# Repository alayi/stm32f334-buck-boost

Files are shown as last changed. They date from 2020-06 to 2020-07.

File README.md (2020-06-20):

## Buck-boost преобразователь с цифровым управлением

Преобразователь построен на базе микроконтроллера STM32F334C4 с аппаратным модулем HRPWM с возможностью работы на частотах от 100 до 2000 кГц, в зависимости от примененных драйверов и транзисторов. В источнике питания реализованы аппаратные защиты по току и другие, что позволяет значительно повысить надежность работы. Для отладки выведены на разъем интерфейсы SWD и UART-TX, что позволяет производить real-time отладку через средства freeMaster и стандартный printf.

Вид платы (https://habrastorage.org/webt/9y/gj/tb/9ygjtbmnwvxfb2rbhex7k384b44.jpeg)

## Технические характеристики

* Топология: *buck-boost*
* Входное напряжение: *3...15В*
* Выходное напряжение: *3...15В*
* Стабилизация напряжения: *±0,5%*
* Номинальный ток: *5А*
* Стабилизация тока: *±2%* 
* Частота коммутации: *200 кГц*
* Алгоритмы: *CC/CV*
* КПД: *не менее 92%*
* Защиты: *OCP, OVP, UVLO, перегрев*
* Диапазон температур: *-40...+85 <sup>о</sup>C*
* Габариты: *52х50х8 мм*

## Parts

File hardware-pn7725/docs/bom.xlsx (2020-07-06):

Designator | Value | PartNumber | Manufacturer | Quantity | Comment | HelpURL
C1, C2 | 0.47μF | CL21B474KAFNNNG | Samsung | 2 | Ceramic capacitor, 0.47μF, X7R, ±10%, 25V, 805, -55...+125°C | https://www.digikey.com/product-detail/en/samsung-electro-mechanics/CL21B474KAFNNNG/1276-6480-1-ND/5958108
C3, C4, C7, C8 | 10μF | CL32B106KAJNNNE | Samsung | 4 | Ceramic capacitor, 10μF, X7R, ±10%, 25V, 1210, -55...+125°C | https://www.digikey.com/product-detail/en/samsung-electro-mechanics/CL32B106KAJNNNE/1276-1807-1-ND/3889893
C5, C6, C13, C14, C15, C16, C24, C25 | 1μF | CL10B105KA8NNNC | Samsung | 8 | Ceramic capacitor, 1μF, X7R, ±10%, 25V, 603, -55...+125°C | https://www.digikey.com/product-detail/en/samsung-electro-mechanics/CL10B105KA8NNNC/1276-1184-1-ND/3889270
C9, C10, C11, C12, C23 | 0.01μF | CL10B103KB8NNNC | Yageo | 5 | Ceramic capacitor, 0.01μF, X7R, ±10%, 50V, 603, -55...+125°C | https://www.digikey.com/product-detail/en/samsung-electro-mechanics/CL10B103KB8NNNC/1276-1009-1-ND/3889095
C17, C18, C19, C20, C21, C22, C26, C29, C30 | 0.1μF | CL10B104KB8WPND | Yageo | 9 | Ceramic capacitor, 0.1μF, X7R, ±10%, 50V, 603, -55...+125°C | https://www.digikey.com/product-detail/en/samsung-electro-mechanics/CL10B104KB8WPND/1276-CL10B104KB8WPNDCT-ND/11488014
C27, C28 | 12pF | CL10C120JB8NNNC | Samsung | 2 | Ceramic capacitor, 12pF, NPO, ±10%, 50V, 603, -55...+125°C | https://www.digikey.com/product-detail/en/samsung-electro-mechanics/CL10C120JB8NNNC/1276-1254-1-ND/3889340
D1, D2 |  | PN7725 | Chipown | 2 | Half-bridge module, 2N channel, 200kHz, 15W, supply 4...20V, -40...+125°C, 8-SOIC-PAD | http://chipown.com/product.asp?id=416
D3, D4 |  | INA199A1DCKR | Texas Instruments | 2 | IC current monitor, ±1.5%, 50V/V, -0.3...+26V, -40...+125°C, SOT23-5 | https://www.digikey.com/product-detail/en/texas-instruments/INA199A1DCKR/296-27329-1-ND/2279290
D5 |  | AP3012KTR-G1 | Diodes Incorporated | 1 | DC/DC boost converter, input 2.6...16V, 1.5MHz, output 3...29V, 0.5A, -40...+85°C, SOT23-5 | https://www.digikey.com/product-detail/en/diodes-incorporated/AP3012KTR-G1/AP3012KTR-G1DICT-ND/4505297
D6 |  | AP2204K-3.3TRG1 | Diodes Incorporated | 1 | Linear voltage regulator, input 4...24V, 0.5V, output 3.3V, 0.15A, -40...+85°C, SOT23-6 | https://www.digikey.com/product-detail/en/diodes-incorporated/AP2204K-3.3TRG1/AP2204K-3.3TRG1DICT-ND/4505288
D7 |  | STM32F334C4T6 | STMicroelectronics | 1 | IC microcontroller, 32-Bit, Cortex-M4, 72MHz, 16KB, 12KB, 2...3.6V, -40...+85°C, 48-LQFP | https://www.digikey.com/products/en?keywords=STM32F334C4T6
D8 |  | AP2204K-5.0TRG1 | Diodes Incorporated | 1 | Linear voltage regulator, input 4...24V, 0.5V, output 5V, 0.15A, -40...+85°C, SOT23-6 | https://www.digikey.com/product-detail/en/diodes-incorporated/AP2204K-5-0TRG1/AP2204K-5-0TRG1DICT-ND/4505289
L1 | 10μH | SDR1006-100ML | Bourns | 1 | Fixed inductor, 10μH, ±20%, SDR0805, 2.6A, -40...+125°C | https://www.digikey.com/product-detail/en/bourns-inc/SDR1006-100ML/SDR1006-100MLCT-ND/2127202
L2 | 10μH | SDR0403-100ML | Bourns | 1 | Fixed inductor, 10μH, ±20%, SDR0403, 1.15A, -40...+125°C | https://www.digikey.com/product-detail/en/bourns-inc/SDR0403-100ML/SDR0403-100MLCT-ND/2127080
L3 | 10μH | LQM18FN100M00D | Murata Electronics | 1 | Fixed inductor, 10μH, ±20%, 603, 50mA, -55...+125°C | https://www.digikey.com/product-detail/en/murata-electronics-north-america/LQM18FN100M00D/490-4025-1-ND/1016285
R5, R9 | 0R015 | PE2512FKE7W0R015L | Yageo | 2 | Resistor film, 0R015, ±1%, 2512, 2W, -55...+170°C | https://www.digikey.com/product-detail/en/yageo/PE2512FKE7W0R015L/YAG2165CT-ND/5139613
R6, R7 | 39k | RC0603FR-0739KL | Yageo | 2 | Resistor film, 39k, ±1%, 603, 0.1W, -55...+125°C | https://www.digikey.com/product-detail/en/yageo/RC0603FR-0739KL/311-39-0KHRCT-ND/730142
R8, R10 | 120R | RC0603JR-07120RL | Yageo | 2 | Resistor film, 120R, ±5%, 603, 0.1W, -55...+125°C | https://www.digikey.com/product-detail/en/yageo/RC0603JR-07120RL/311-120GRCT-ND/729653
R11, R12, R16 | 10k | RC0603FR-0710KL | Yageo | 3 | Resistor film, 10k, ±1%, 603, 0.1W, -55...+125°C | https://www.digikey.com/product-detail/en/yageo/RC0603FR-0710KL/311-10-0KHRCT-ND/729827
R13, R15, R19, R20, R21 | 10k | RC0603JR-0710KL | Yageo | 5 | Resistor film, 10k, ±5%, 603, 0.1W, -55...+125°C | https://www.digikey.com/product-detail/en/yageo/RC0603JR-0710KL/311-10KGRCT-ND/729647
R14 | 110k | RC0603FR-07110KL | Yageo | 1 | Resistor film, 110k, ±1%, 603, 0.1W, -55...+125°C | https://www.digikey.com/product-detail/en/yageo/RC0603FR-07110KL/311-110KHRCT-ND/729852
R17, R18 | 1k | RC0603FR-071KL | Yageo | 2 | Resistor film, 1k, ±1%, 603, 0.1W, -55...+125°C | https://www.digikey.com/product-detail/en/yageo/RC0603FR-071KL/311-1-00KHRCT-ND/729790
VD1 |  | B160S1F-7 | Diodes Incorporated | 1 | Schottky diode, 60B160S1F-7, 1A, 650mV, 45pF, SOD-123F, -55...+150°C | https://www.digikey.com/product-detail/en/diodes-incorporated/B160S1F-7/B160S1F-7DICT-ND/7784161
VD2 |  | 150060BS75000 | Wurth | 1 | LED, 20mA, 3.2V, 603, -55...+150°C | https://www.digikey.com/product-detail/en/w-rth-elektronik/150060BS75000/732-4966-1-ND/4489893
VD3 |  | 150060RS75000 | Wurth | 1 | LED, 20 mA, 2V, 603, -55...+150°C | https://www.digikey.com/product-detail/en/w-rth-elektronik/150060RS75000/732-4978-1-ND/4489899
X1, X2, X3, X4 |  | 8191 | Keystone | 4 | Power connector, 500V, 15A | https://ru.mouser.com/ProductDetail/Keystone-Electronics/8191?qs=lQmX4aIt5iAMQ8PQTpZ%2Fwg%3D%3D
X5 |  | SM05B-GHS | JST | 1 | Connector, 5pin, 1.25mm, 50VDC, 1A | https://www.digikey.com/product-detail/en/jst-sales-america-inc/SM05B-GHS-TB-LF-SN/455-1567-1-ND/807835
Z1 |  | ECS-80-12-33-JGN-TR | ECS | 1 | Crystal, 8MHz, 12pF, ±30ppm, case 3225, -40...+85°C | https://www.digikey.com/product-detail/en/ecs-inc/ECS-80-12-33-JGN-TR/50-ECS-80-12-33-JGN-CT-ND/10478769

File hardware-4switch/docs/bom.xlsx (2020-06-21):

Designator | Value | PartNumber | Manufacturer | Quantity | Comment | HelpURL
C1, C2 | 0.47μF | CL21B474KAFNNNG | Samsung | 2 | Ceramic capacitor, 0.47μF, X7R, ±10%, 25V, 0805, -55...+125°C | https://www.digikey.com/product-detail/en/samsung-electro-mechanics/CL21B474KAFNNNG/1276-6480-1-ND/5958108
C3, C4, C17, C18, C19, C20, C26, C27 | 1μF | CL10B105KA8NNNC | Samsung | 8 | Ceramic capacitor, 1μF, X7R, ±10%, 25V, 0603, -55...+125°C | https://www.digikey.com/product-detail/en/samsung-electro-mechanics/CL10B105KA8NNNC/1276-1184-1-ND/3889270
C5, C6, C7, C8, C9, C10 | 10μF | CL32B106KAJNNNE | Samsung | 6 | Ceramic capacitor, 10μF, X7R, ±10%, 25V, 1210, -55...+125°C | https://www.digikey.com/product-detail/en/samsung-electro-mechanics/CL32B106KAJNNNE/1276-1807-1-ND/3889893
C11, C12, C15, C16, C25 | 0.01μF | CL10B103KB8NNNC | Yageo | 5 | Ceramic capacitor, 0.01μF, X7R, ±10%, 50V, 0603, -55...+125°C | https://www.digikey.com/product-detail/en/samsung-electro-mechanics/CL10B103KB8NNNC/1276-1009-1-ND/3889095
C13, C14 | 470pF | CL10C471JB8NNNC | Yageo | 2 | Ceramic capacitor, 470pF, NPO, ±5%, 50V, 0603, -55...+125°C | https://www.digikey.com/product-detail/en/samsung-electro-mechanics/CL10C471JB8NNNC/1276-1168-1-ND/3889254
C21, C22, C23, C24, C28, C31, C32 | 0.1μF | CL10B104KB8WPND | Yageo | 7 | Ceramic capacitor, 0.1μF, X7R, ±10%, 50V, 0603, -55...+125°C | https://www.digikey.com/product-detail/en/samsung-electro-mechanics/CL10B104KB8WPND/1276-CL10B104KB8WPNDCT-ND/11488014
C29, C30 | 12pF | CL10C120JB8NNNC | Samsung | 2 | Ceramic capacitor, 12pF, NPO, ±10%, 50V, 0603, -55...+125°C | https://www.digikey.com/product-detail/en/samsung-electro-mechanics/CL10C120JB8NNNC/1276-1254-1-ND/3889340
D1, D2 |  | FD2105M | Fortior Tech | 2 | Half-bridge gate driver, 40V, +1.2A/-1.8A, Complementary, supply 3...21V, -40...+125°C, 10-MSOP | https://lcsc.com/product-detail/Others_Fortior-Tech-FD2105M_C328452.html
D3, D4 |  | TSV991ILT | STMicroelectronics | 2 | IC op amplifier, Rail-to-Rail, 20 MHz, 2.7...5.5V, -40...+125°C, SOT23-5 | https://www.digikey.com/product-detail/en/stmicroelectronics/TSV991ILT/497-6001-1-ND/1578484
D5 |  | AP3012KTR-G1 | Diodes Incorporated | 1 | DC/DC boost converter, input 2.6...16V, 1.5MHz, output 3...29V, 0.5A, -40...+85°C, SOT23-5 | https://www.digikey.com/product-detail/en/diodes-incorporated/AP3012KTR-G1/AP3012KTR-G1DICT-ND/4505297
D6 |  | STM32F334C4T6 | STMicroelectronics | 1 | IC microcontroller, 32-Bit, Cortex-M4, 72MHz, 16KB, 12KB, 2...3.6V, -40...+85°C, 48-LQFP | https://www.digikey.com/products/en?keywords=STM32F334C4T6
D7 |  | AP2204K-3.3TRG1 | Diodes Incorporated | 1 | Linear voltage regulator, input 4...24V, 0.5V, output 3.3V, 0.15A, -40...+85°C, SOT23-6 | https://www.digikey.com/product-detail/en/diodes-incorporated/AP2204K-3.3TRG1/AP2204K-3.3TRG1DICT-ND/4505288
L1 | 10μH | SRP1038C-100M | Bourns | 1 | Fixed inductor, 10μH, ±20%, SRP1038C, 8.5A, -40...+125°C | https://www.digikey.com/product-detail/en/bourns-inc/SRP1038C-100M/SRP1038C-100MCT-ND/10249149
L2 | 10μH | SDR0403-100ML | Bourns | 1 | Fixed inductor, 10μH, ±20%, SDR0403, 1.15A, -40...+125°C | https://www.digikey.com/product-detail/en/bourns-inc/SDR0403-100ML/SDR0403-100MLCT-ND/2127080
L3 | 10μH | LQM18FN100M00D | Murata Electronics | 1 | Fixed inductor, 10μH, ±20%, 0603, 50mA, -55...+125°C | https://www.digikey.com/product-detail/en/murata-electronics-north-america/LQM18FN100M00D/490-4025-1-ND/1016285
R1, R2, R5, R6 | 10R | RC0603JR-0710RL | Yageo | 4 | Resistor film, 10R, ±5%, 0603, 0.1W, -55...+125°C | https://www.digikey.com/product-detail/en/yageo/RC0603JR-0710RL/311-10GRCT-ND/729646
R3, R4, R7, R8, R11, R12, R13, R14, R35, R42, R43, R46 | 10k | RC0603JR-0710KL | Yageo | 12 | Resistor film, 10k, ±5%, 0603, 0.1W, -55...+125°C | https://www.digikey.com/product-detail/en/yageo/RC0603JR-0710KL/311-10KGRCT-ND/729647
R9, R10 | 120k | RC0603JR-07120KL | Yageo | 2 | Resistor film, 120k, ±5%, 0603, 0.1W, -55...+125°C | https://www.digikey.com/product-detail/en/yageo/RC0603JR-07120KL/311-120KGRCT-ND/729654
R15, R16 | 39k | RC0603FR-0739KL | Yageo | 2 | Resistor film, 39k, ±1%, 0603, 0.1W, -55...+125°C | https://www.digikey.com/product-detail/en/yageo/RC0603FR-0739KL/311-39-0KHRCT-ND/730142
R17, R18, R39 | 10k | RC0603FR-0710KL | Yageo | 3 | Resistor film, 10k, ±1%, 0603, 0.1W, -55...+125°C | https://www.digikey.com/product-detail/en/yageo/RC0603FR-0710KL/311-10-0KHRCT-ND/729827
R19, R20, R33, R34 | 20k | RC0603FR-0720KL | Yageo | 4 | Resistor film, 20k, ±1%, 0603, 0.1W, -55...+125°C | https://www.digikey.com/product-detail/en/yageo/RC0603FR-0720KL/311-20-0KHRCT-ND/729987
R21, R22, R23, R24, R29, R30, R31, R32, R36, R37, R40, R41, R44, R45 | 1k | RC0603FR-071KL | Yageo | 14 | Resistor film, 1k, ±1%, 0603, 0.1W, -55...+125°C | https://www.digikey.com/product-detail/en/yageo/RC0603FR-071KL/311-1-00KHRCT-ND/729790
R25, R26 | 120R | RC0603JR-07120RL | Yageo | 2 | Resistor film, 120R, ±5%, 0603, 0.1W, -55...+125°C | https://www.digikey.com/product-detail/en/yageo/RC0603JR-07120RL/311-120GRCT-ND/729653
R27, R28 | 0R05 | CRA2512-FZ-R050ELF | Bourns | 2 | Resistor film, 0R05, ±1%, 2512, 3W, -55...+170°C | https://www.digikey.com/product-detail/en/bourns-inc/CRA2512-FZ-R050ELF/CRA2512-FZ-R050ELFCT-ND/1775057
R38 | 110k | RC0603FR-07110KL | Yageo | 1 | Resistor film, 110k, ±1%, 0603, 0.1W, -55...+125°C | https://www.digikey.com/product-detail/en/yageo/RC0603FR-07110KL/311-110KHRCT-ND/729852
VD1, VD2, VD3 |  | B160S1F-7 | Diodes Incorporated | 3 | Schottky diode, 60B160S1F-7, 1A, 650mV, 45pF, SOD-123F, -55...+150°C | https://www.digikey.com/product-detail/en/diodes-incorporated/B160S1F-7/B160S1F-7DICT-ND/7784161
VD4, VD5 |  | 150060VS75000 | Wurth | 2 | LED, 20mA, 2V, 0603, -55...+150°C | https://www.digikey.com/product-detail/en/w-rth-elektronik/150060VS75000/732-4980-1-ND/4489904
VD6 |  | 150060BS75000 | Wurth | 1 | LED, 20mA, 3.2V, 0603, -55...+150°C | https://www.digikey.com/product-detail/en/w-rth-elektronik/150060BS75000/732-4966-1-ND/4489893
VD7, VD8, VD9 |  | 150060RS75000 | Wurth | 3 | LED, 20 mA, 2V, 0603, -55...+150°C | https://www.digikey.com/product-detail/en/w-rth-elektronik/150060RS75000/732-4978-1-ND/4489899
VT1, VT2, VT3, VT4 |  | BSC0904NSIATMA1 | Infineon Technologies | 4 | MOSFET N-channel transistor, 30V, 20A, 17nC, 2.5W, 3.7mOhm, 1100pF, 8-TDSON, -55...+150°C | https://www.digikey.com/product-detail/en/infineon-technologies/BSC0904NSIATMA1/BSC0904NSIATMA1CT-ND/3196475
X1, X2, X3, X4 |  | 8191 | Keystone | 4 | Power connector, 500V, 15A | https://ru.mouser.com/ProductDetail/Keystone-Electronics/8191?qs=lQmX4aIt5iAMQ8PQTpZ%2Fwg%3D%3D
X5 |  | SM05B-GHS | JST | 1 | Connector, 5pin, 1.25mm, 50VDC, 1A | https://www.digikey.com/product-detail/en/jst-sales-america-inc/SM05B-GHS-TB-LF-SN/455-1567-1-ND/807835
Z1 |  | ECS-80-12-33-JGN-TR | ECS | 1 | Crystal, 8MHz, 12pF, ±30ppm, case 3225, -40...+85°C | https://www.digikey.com/product-detail/en/ecs-inc/ECS-80-12-33-JGN-TR/50-ECS-80-12-33-JGN-CT-ND/10478769

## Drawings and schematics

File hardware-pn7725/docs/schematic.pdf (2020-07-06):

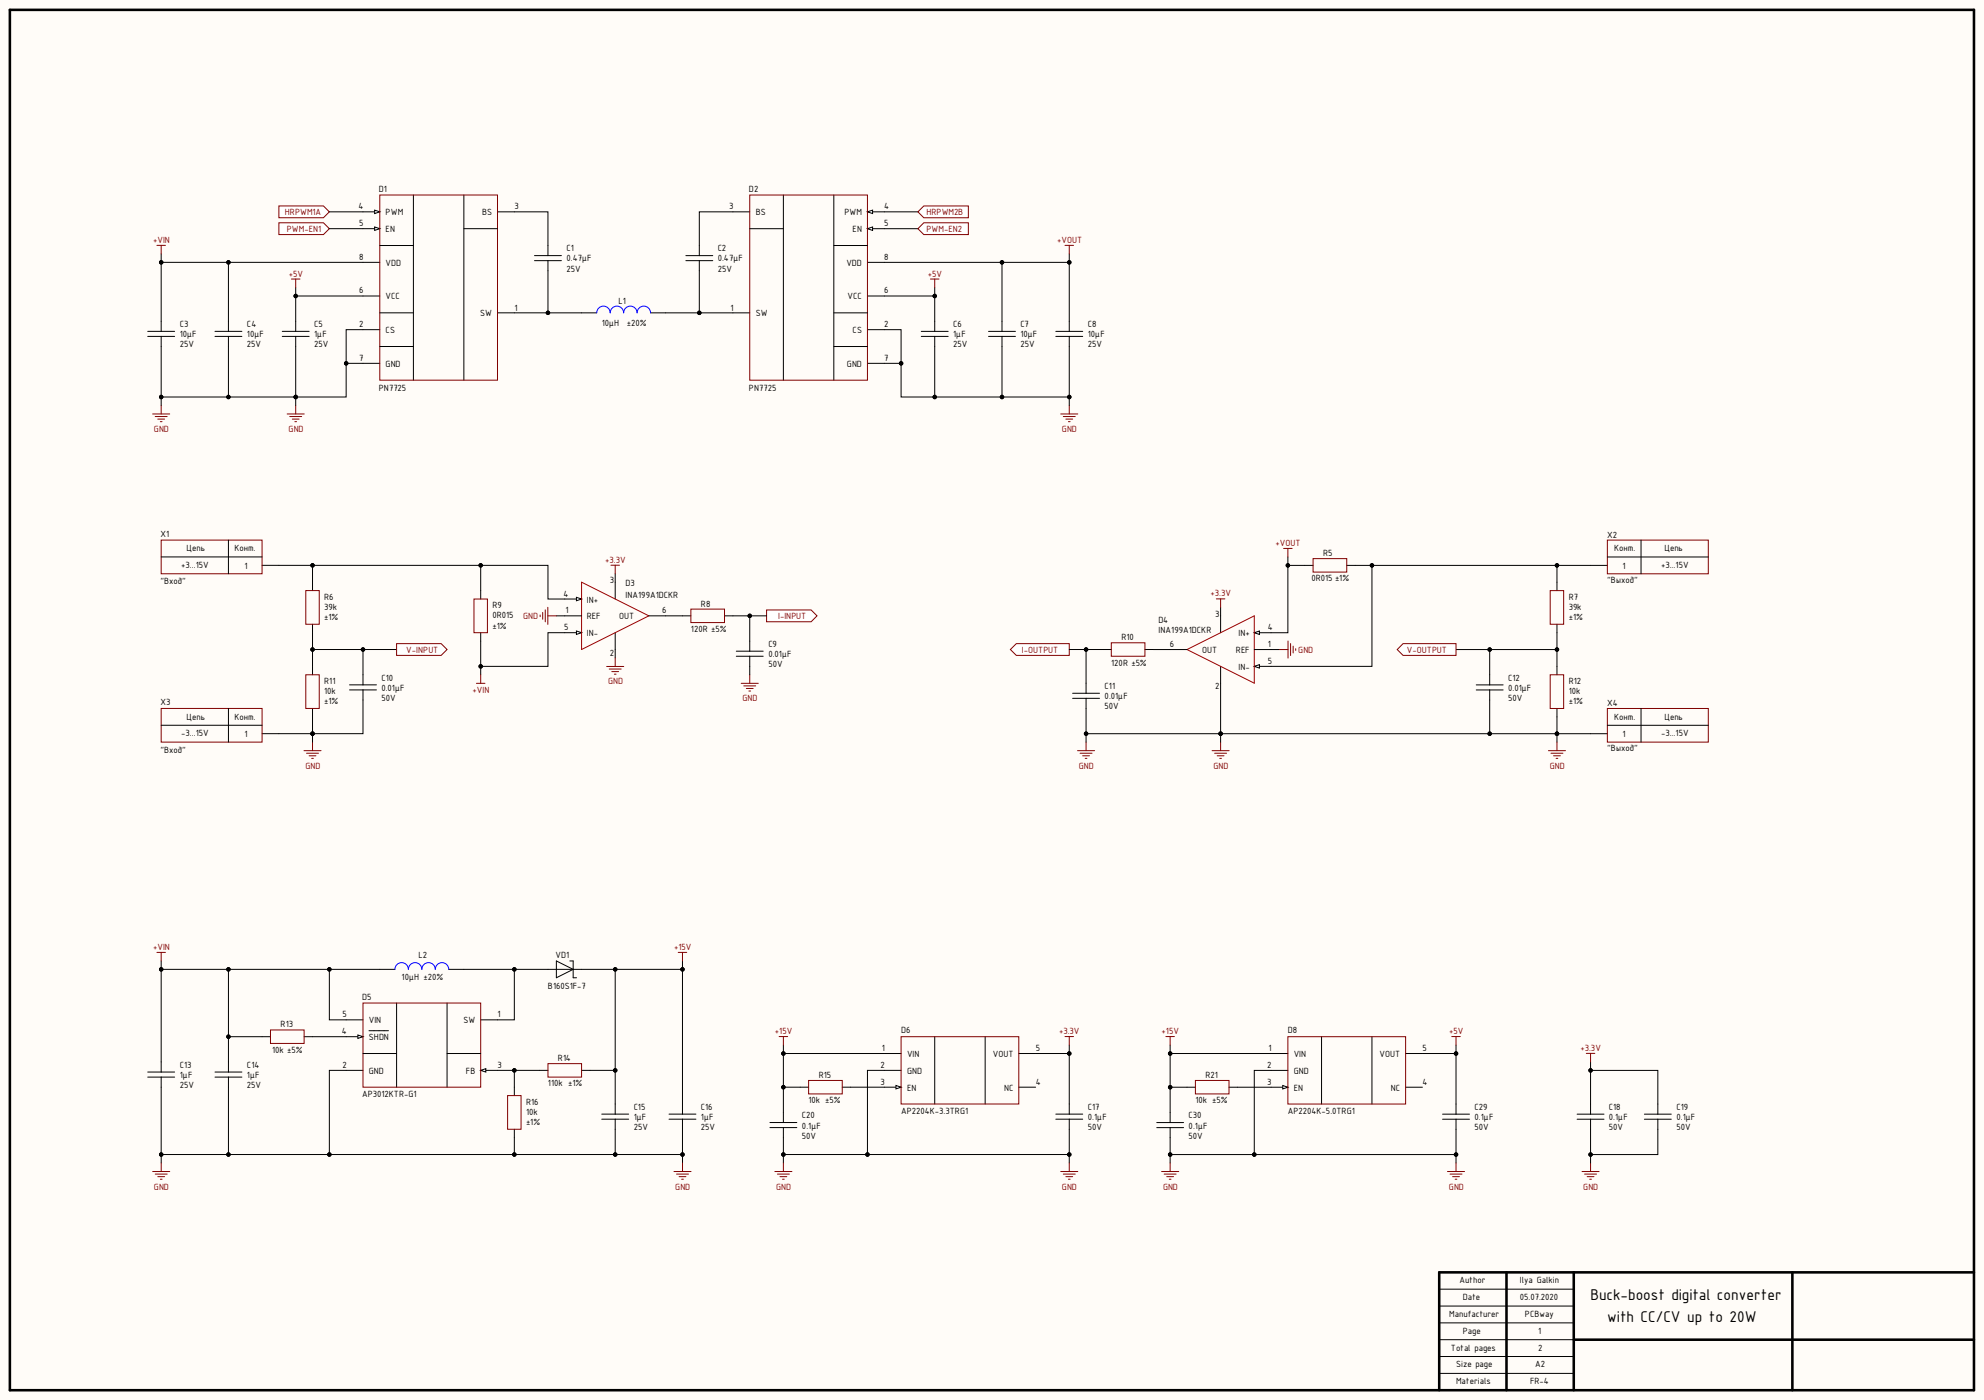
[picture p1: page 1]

Author | Ilya Galkin | Buck-boost digital converter with CC/CV up to 20W

Date | 05.07.2020

Manufacturer | PCBway

Page | 1

Total pages | 2

Size page | A2

Materials | FR-4

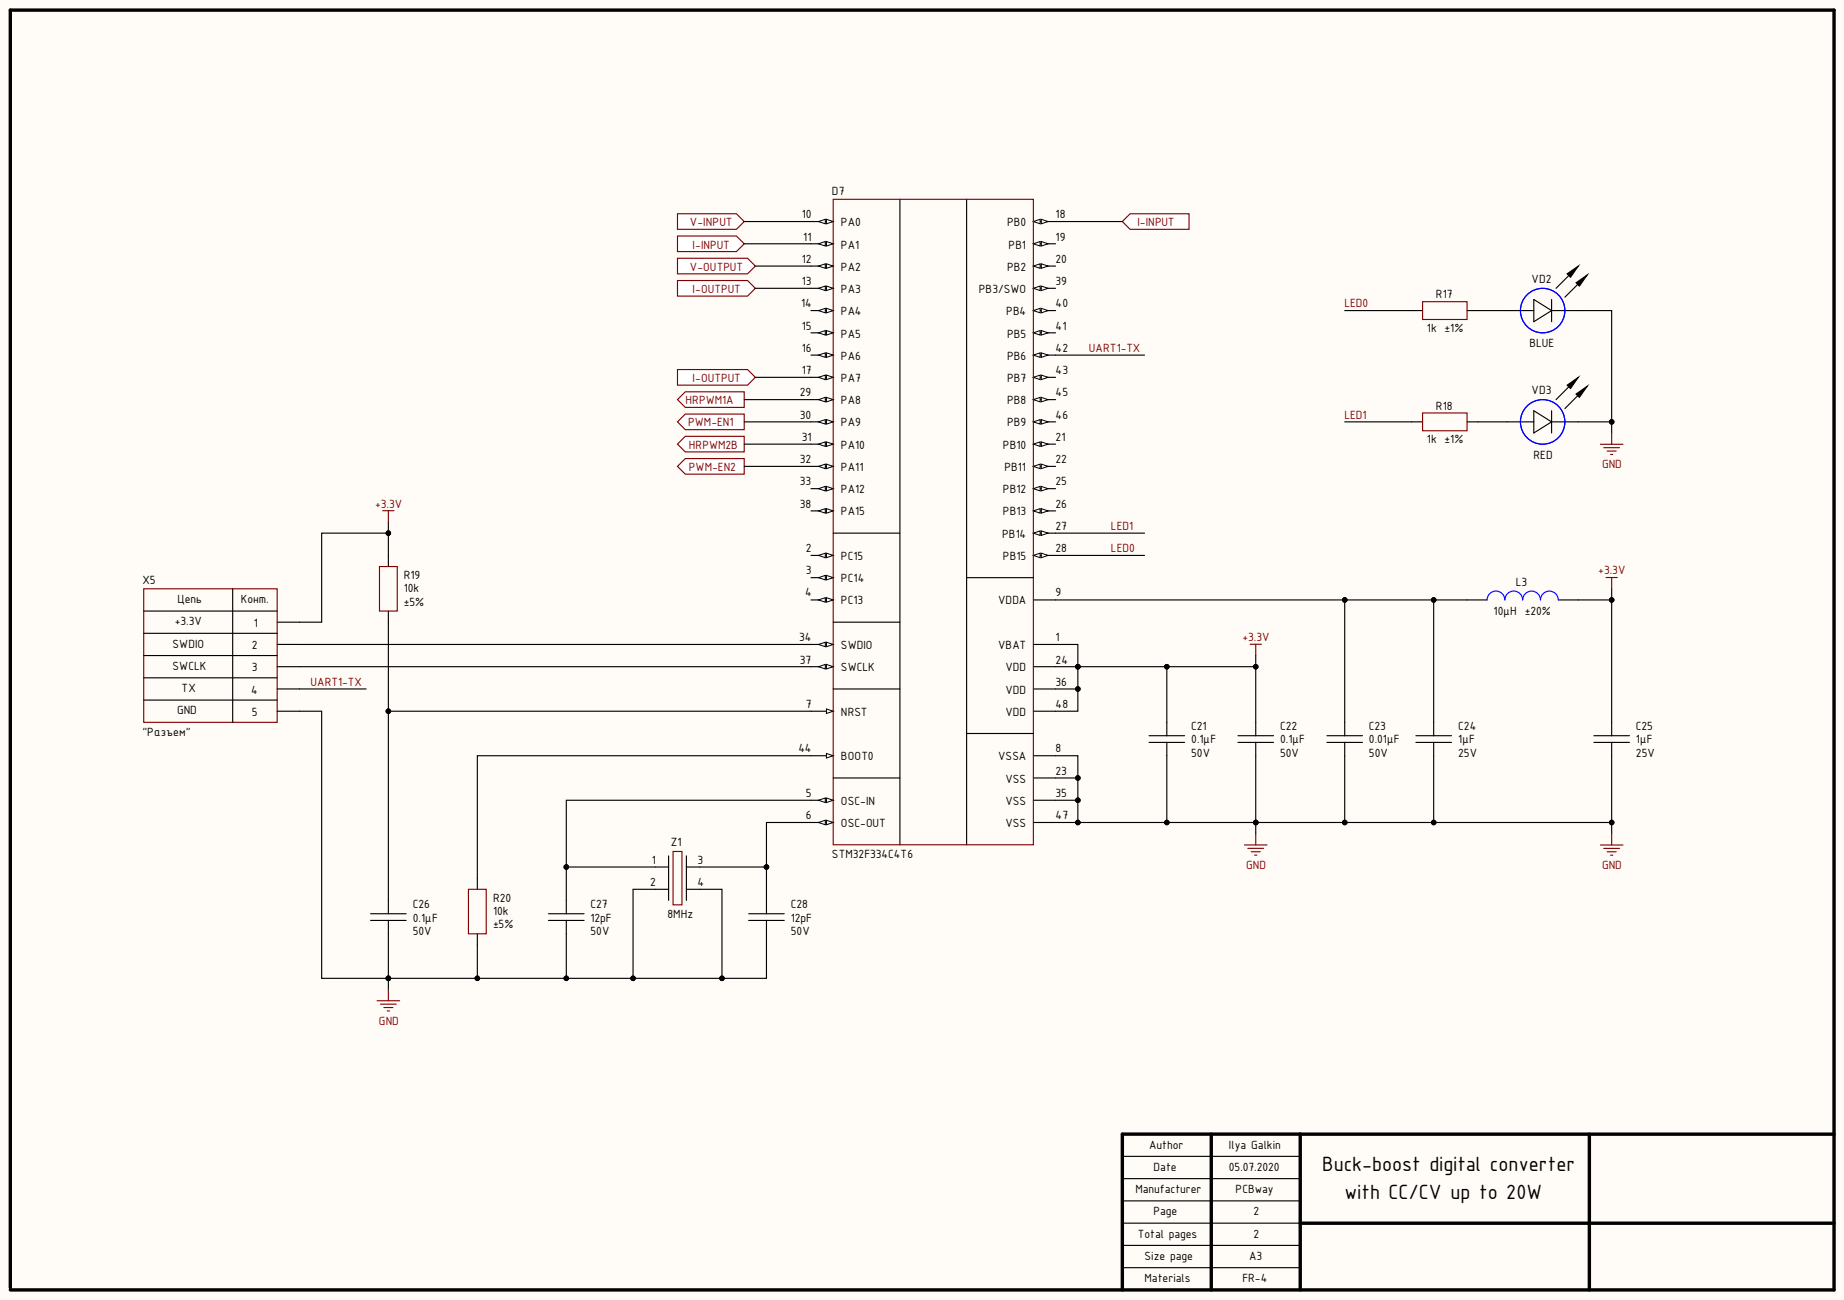
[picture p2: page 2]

Цепь | Конт .

SWCLK SWDIO

Buck-boost digital converter
with CC/CV up to 20W

05.07.2020 PCBway 22

Manufacturer Page Total pages

Materials Size page | A3

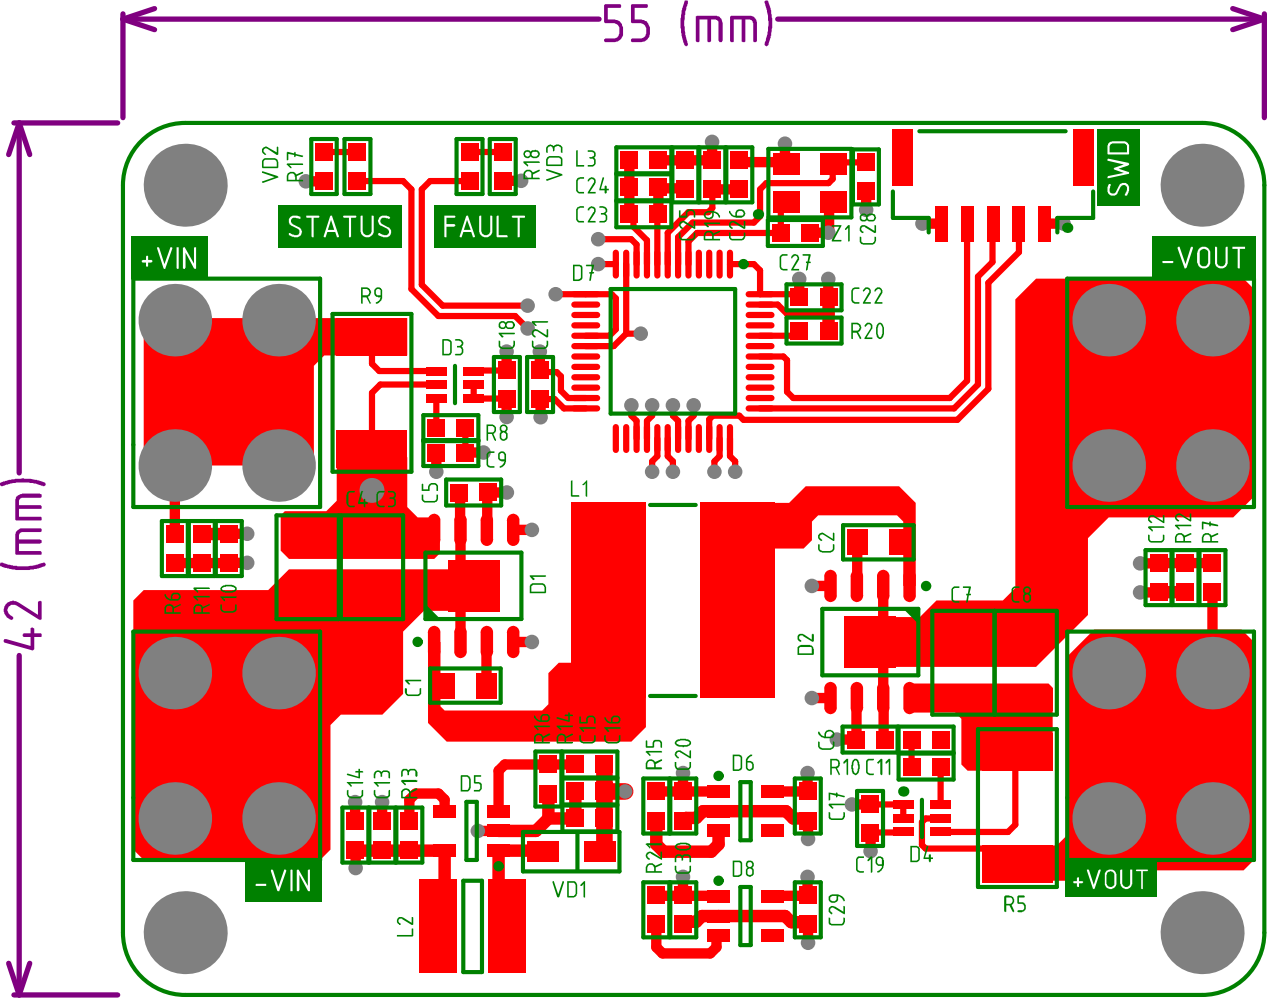
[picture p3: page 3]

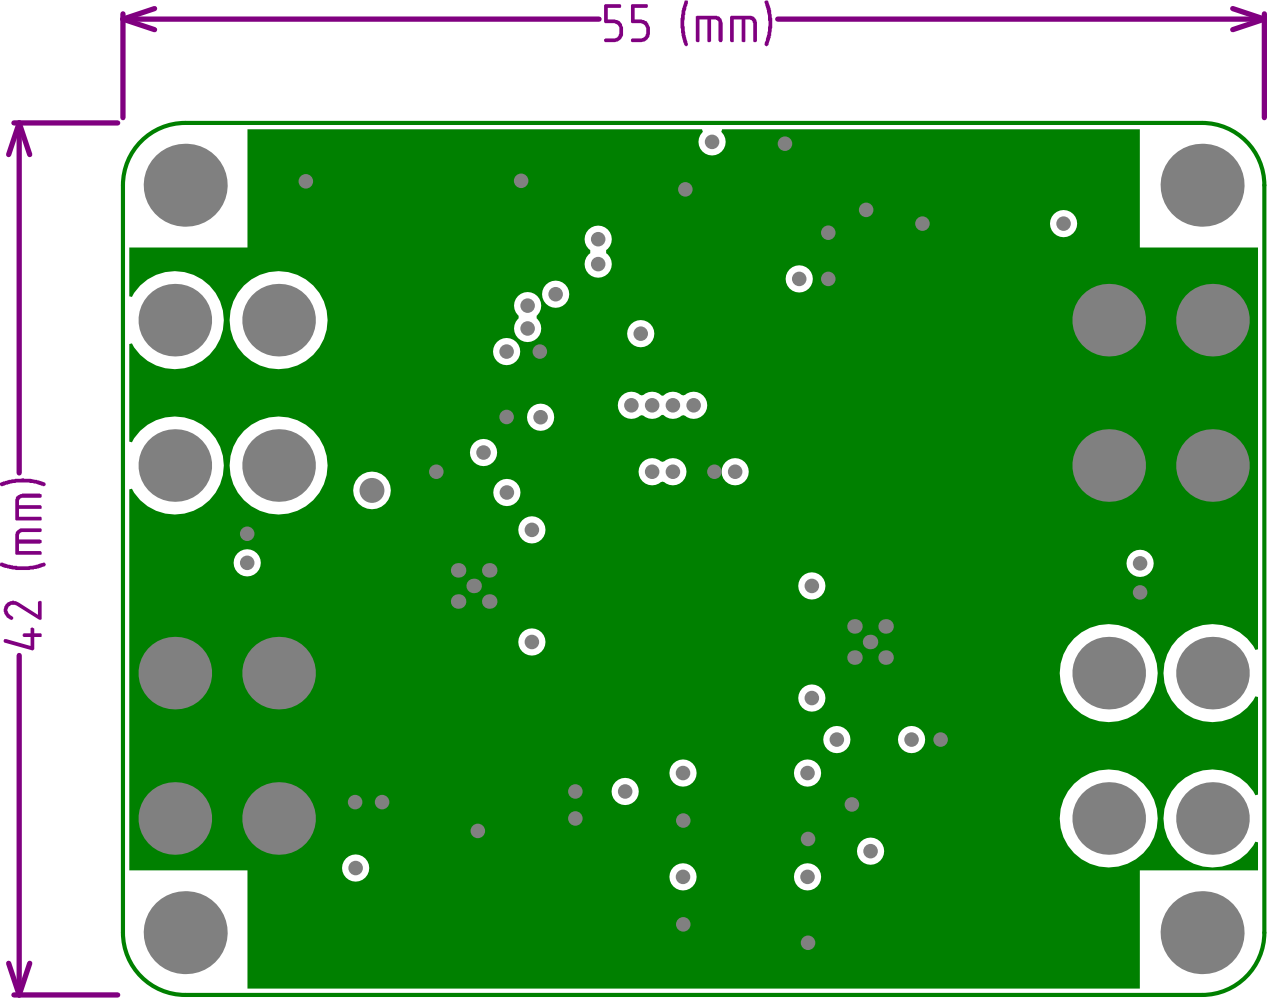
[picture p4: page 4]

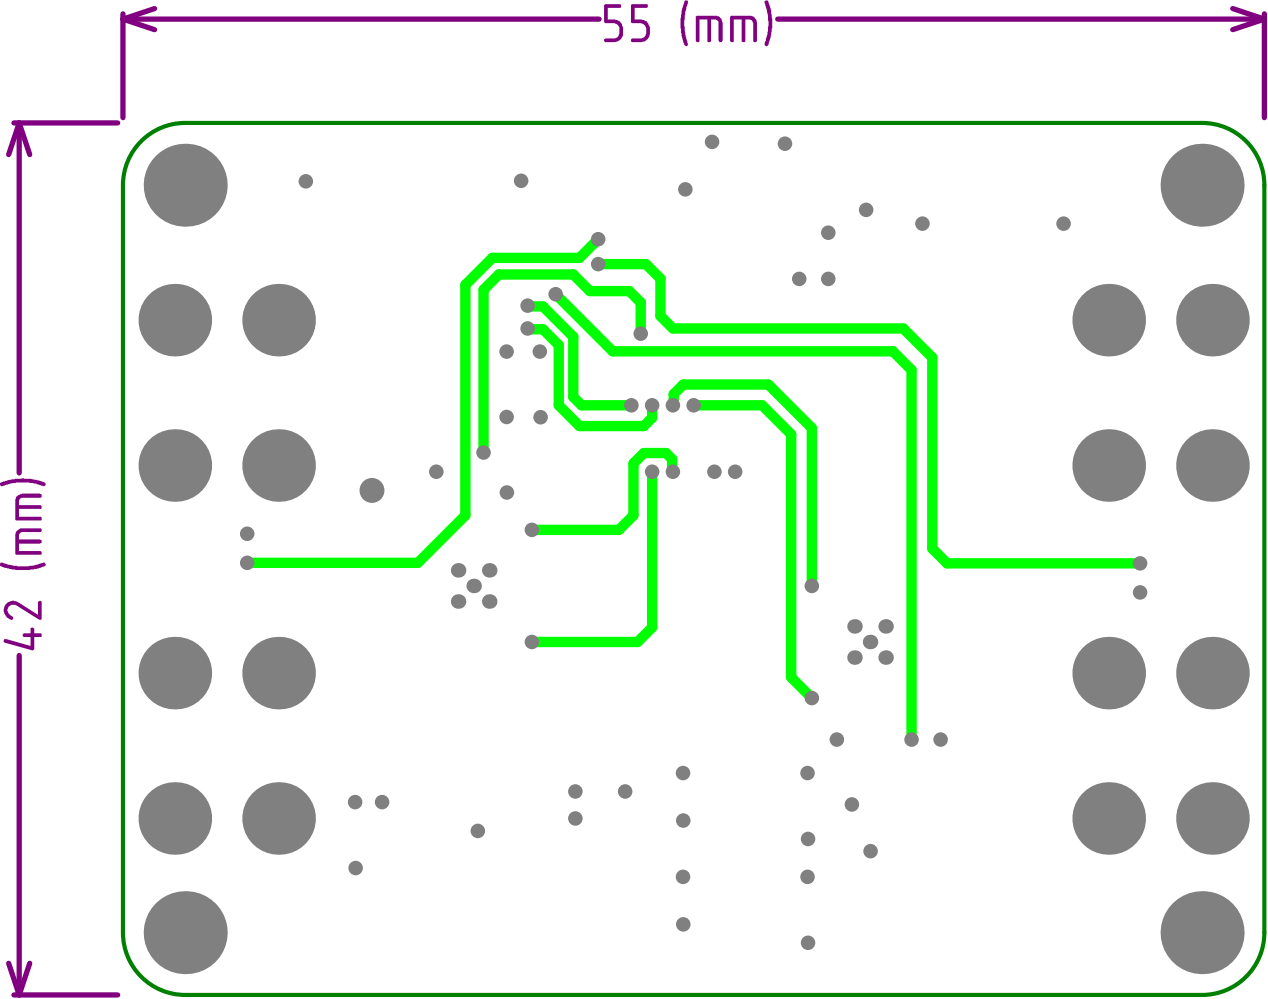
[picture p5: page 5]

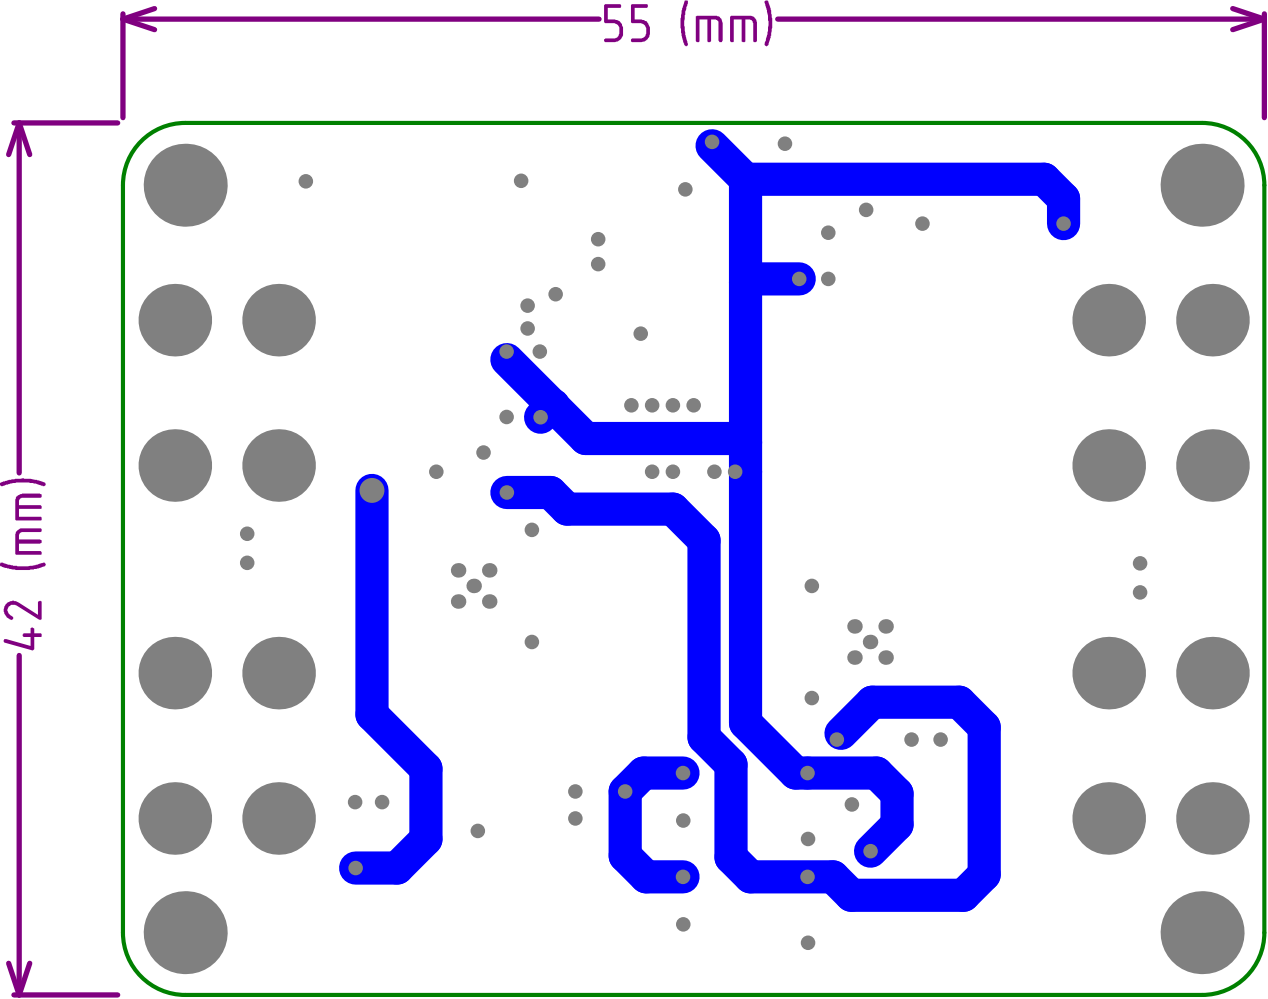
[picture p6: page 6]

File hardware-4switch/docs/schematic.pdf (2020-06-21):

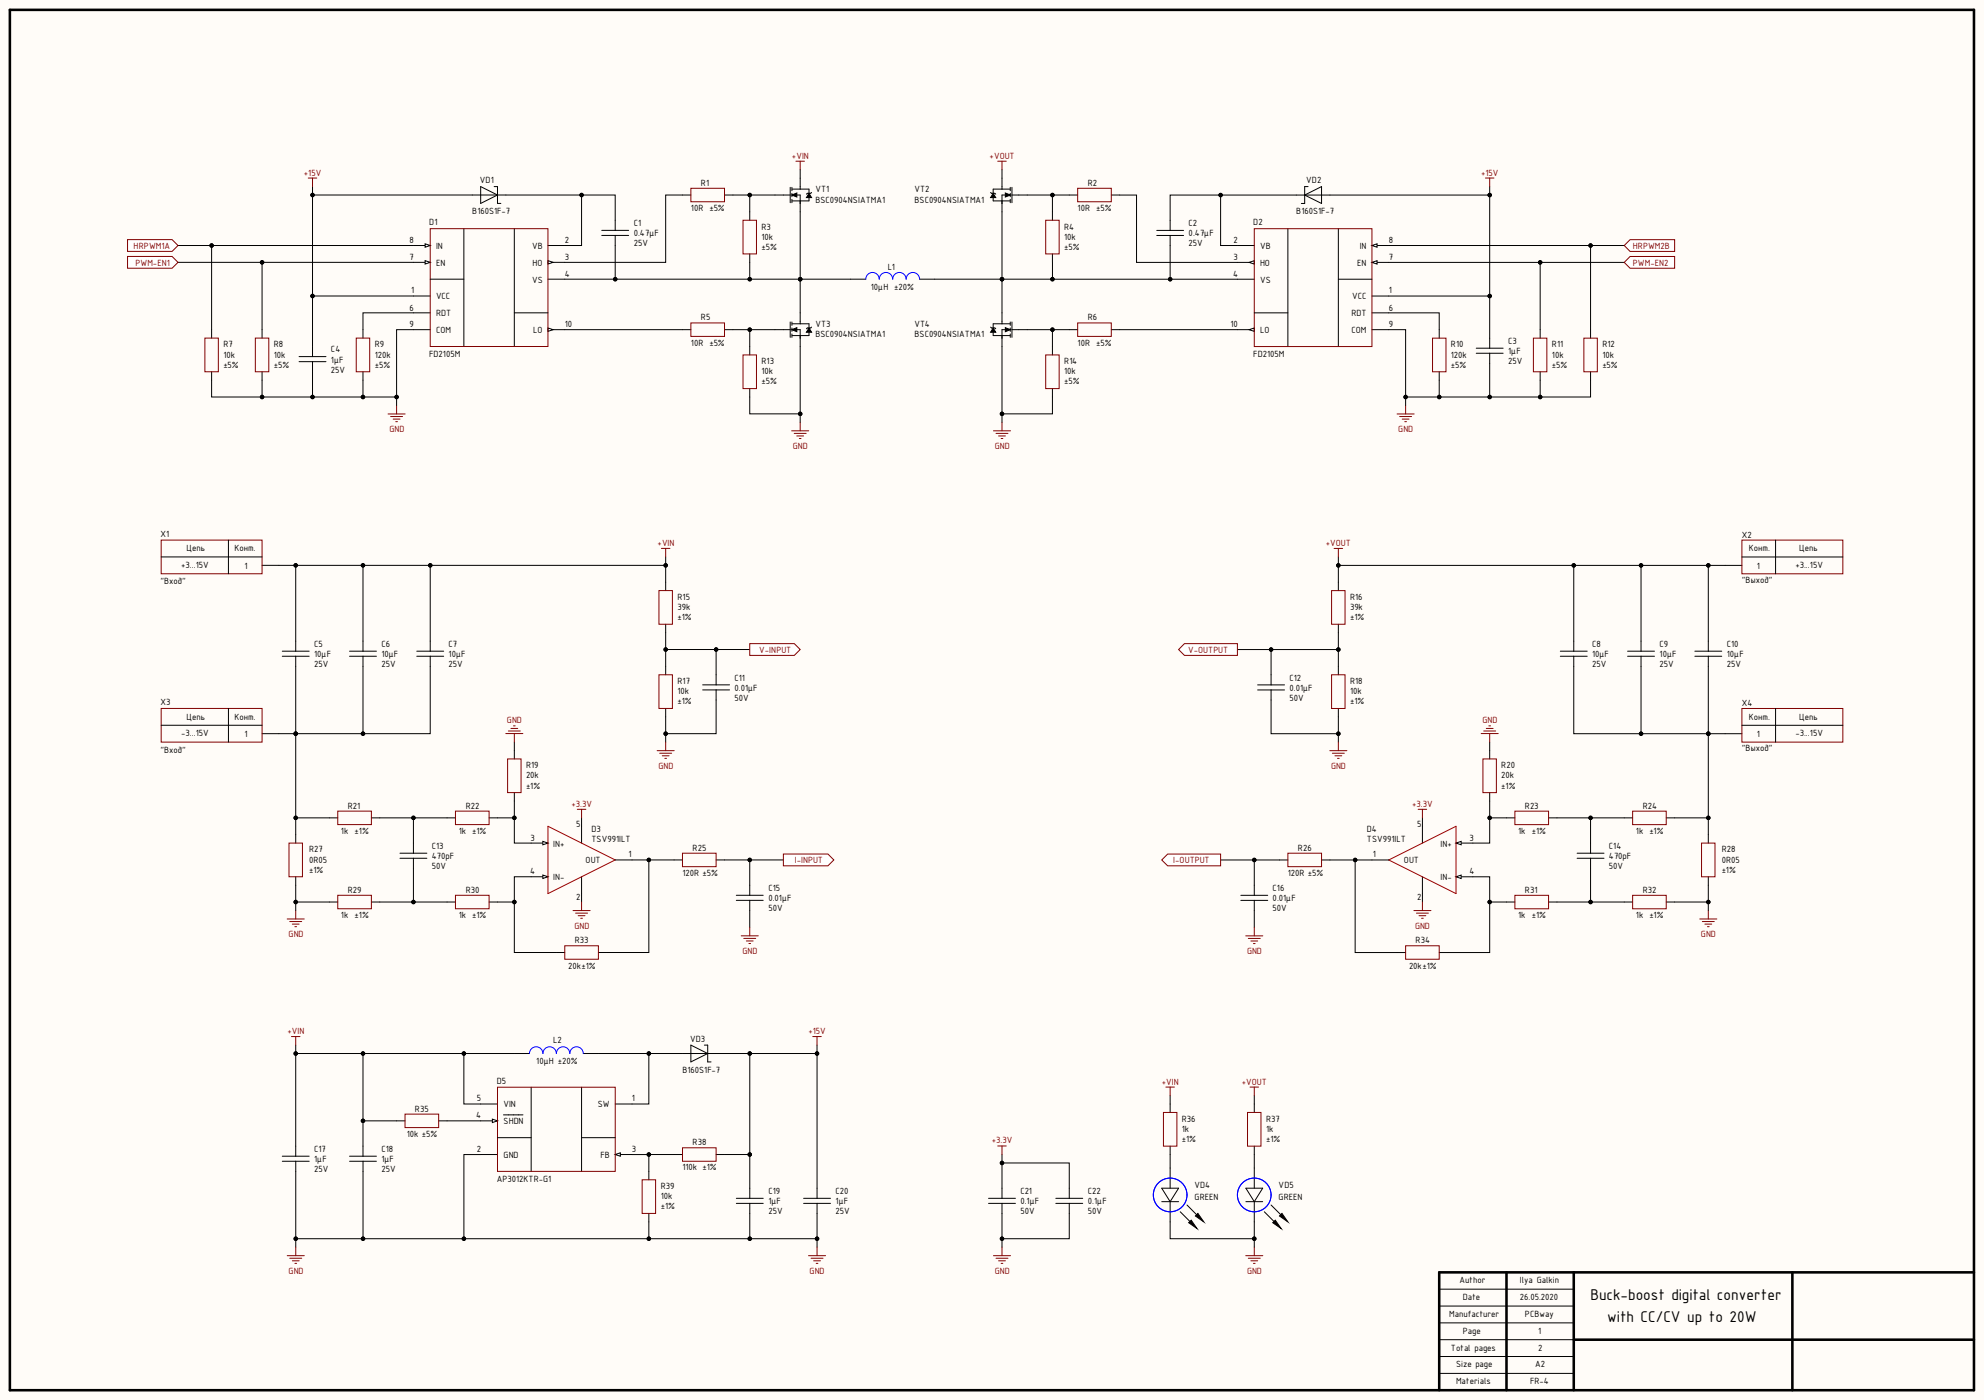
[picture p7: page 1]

Author | Ilya Galkin | Buck-boost digital converter with CC/CV up to 20W

Date | 26.05.2020

Manufacturer | PCBway

Page | 1

Total pages | 2

Size page | A2

Materials | FR-4

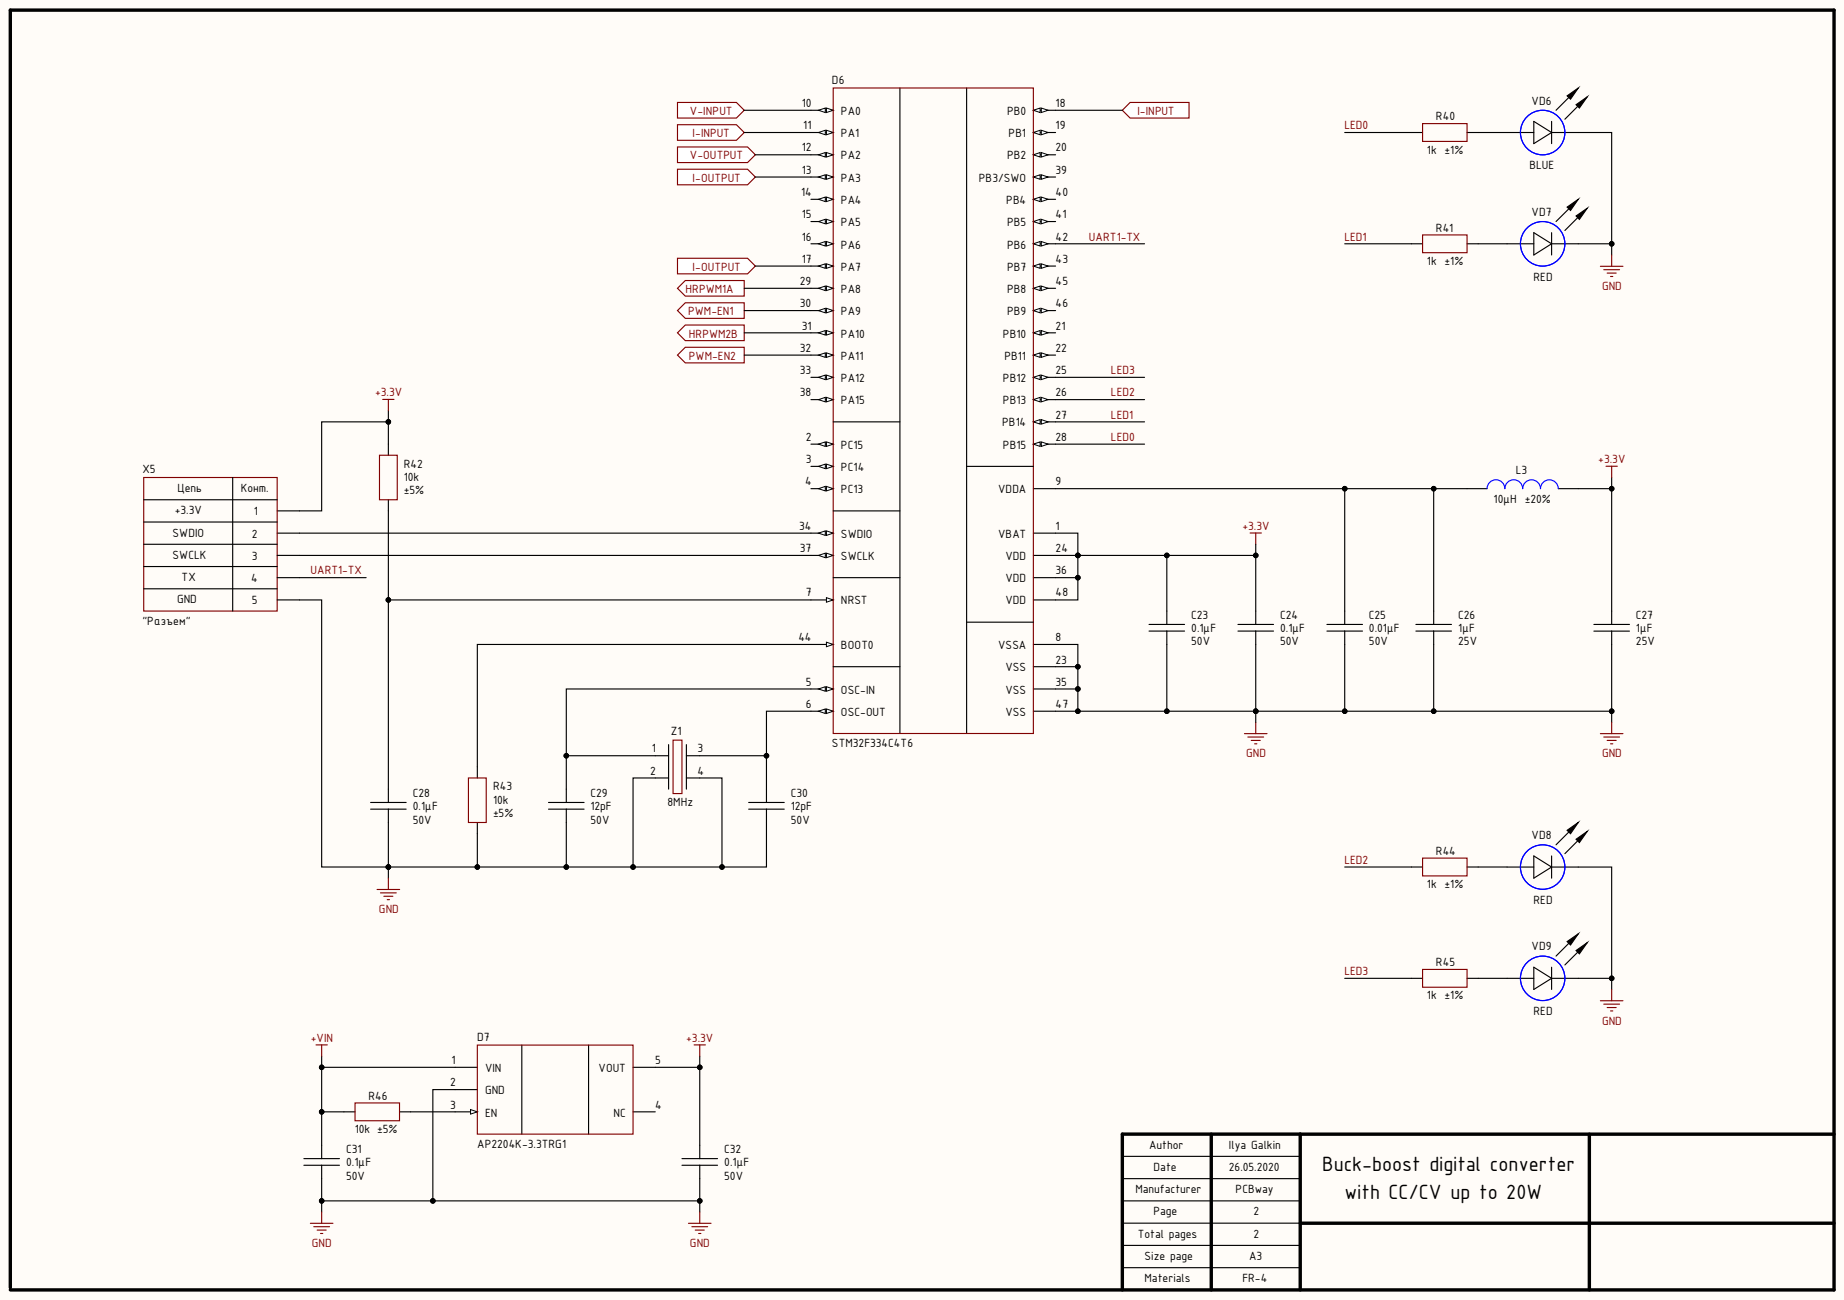
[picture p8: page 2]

Цепь | Конт.

PC13 4 | VDD

SWDIO | 2

SWCLK 37 | 24

SWCLK | 3
4 | UART1-TX TX

NRST 7 | | 36 | 0.1μF

GND | 5

BOOT0 44

Author | Ilya Galkin | Buck-boost digital converter with CC/CV up to 20W

Date | 26.05.2020

Manufacturer | PCBway

Total pages | 2

Size page | A3

Materials | FR-4

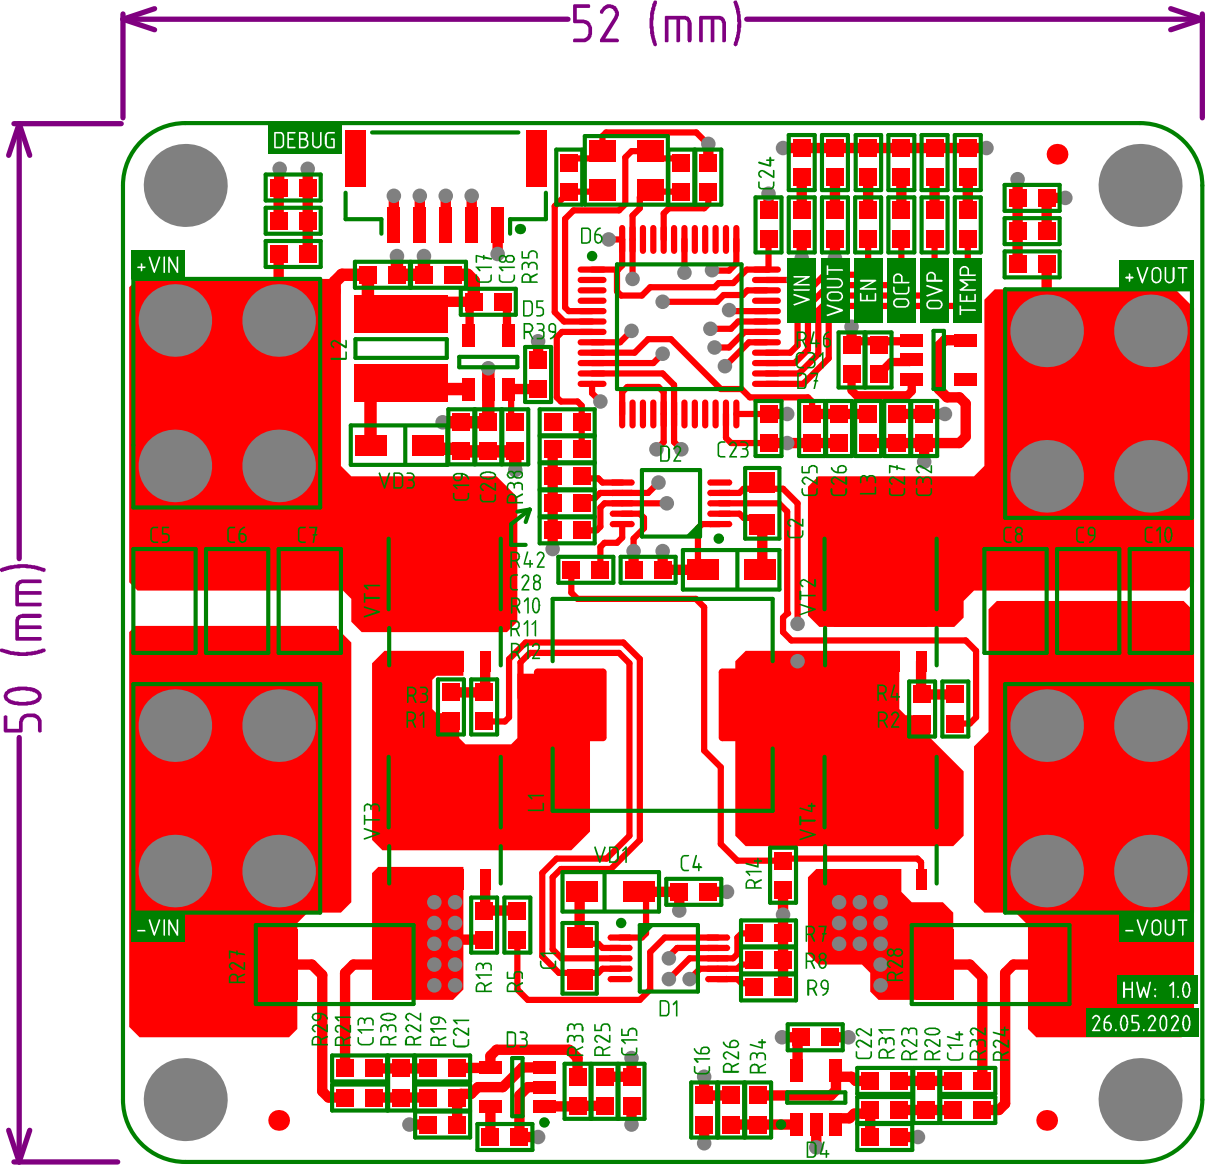
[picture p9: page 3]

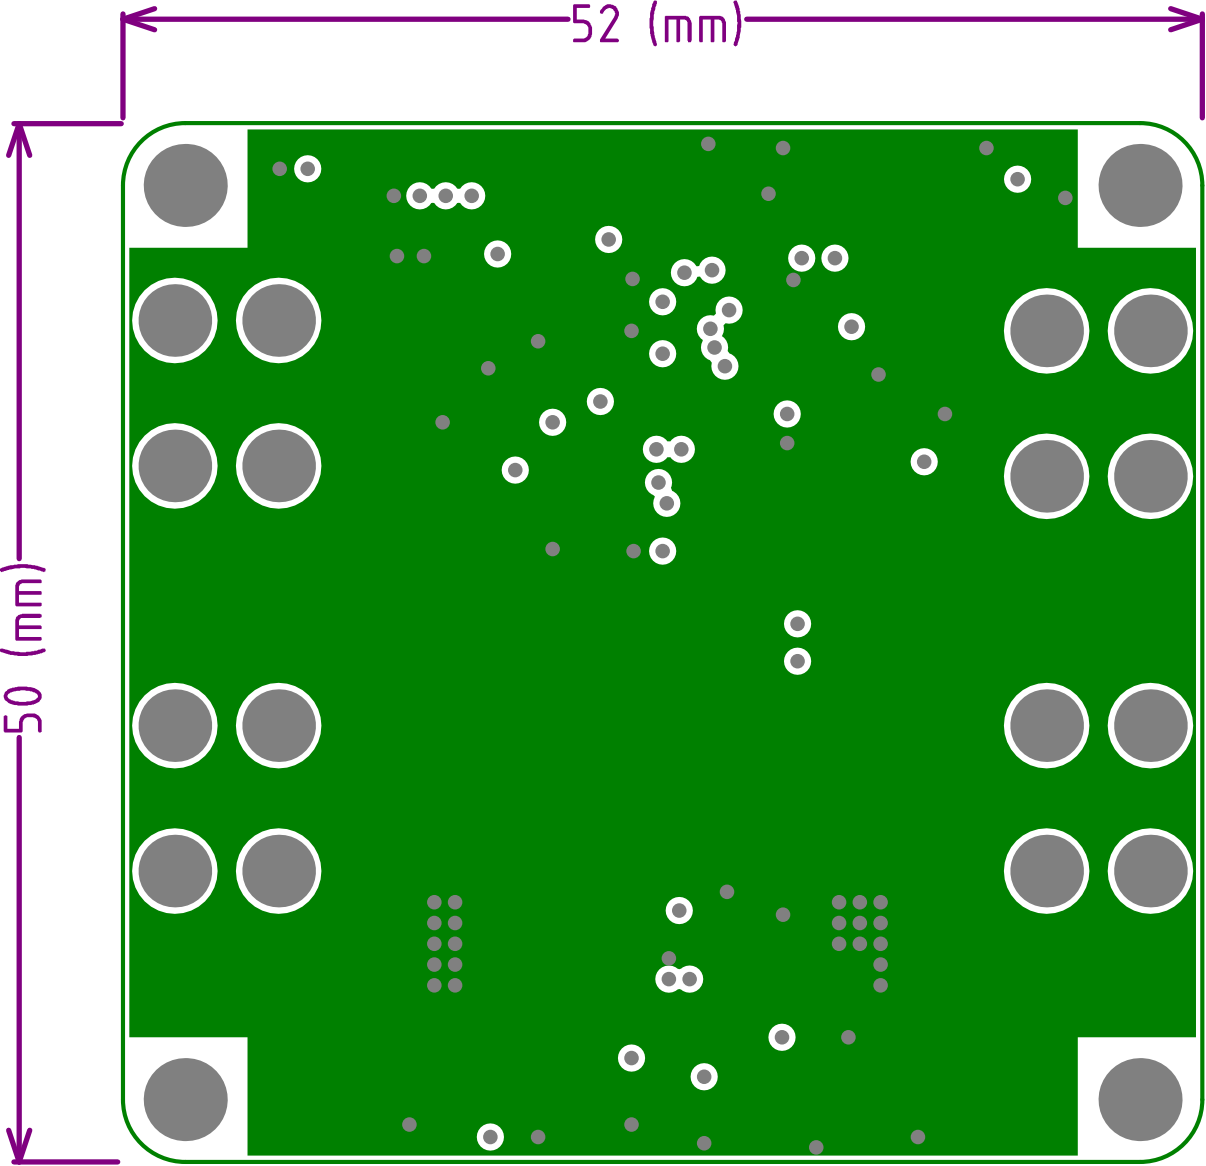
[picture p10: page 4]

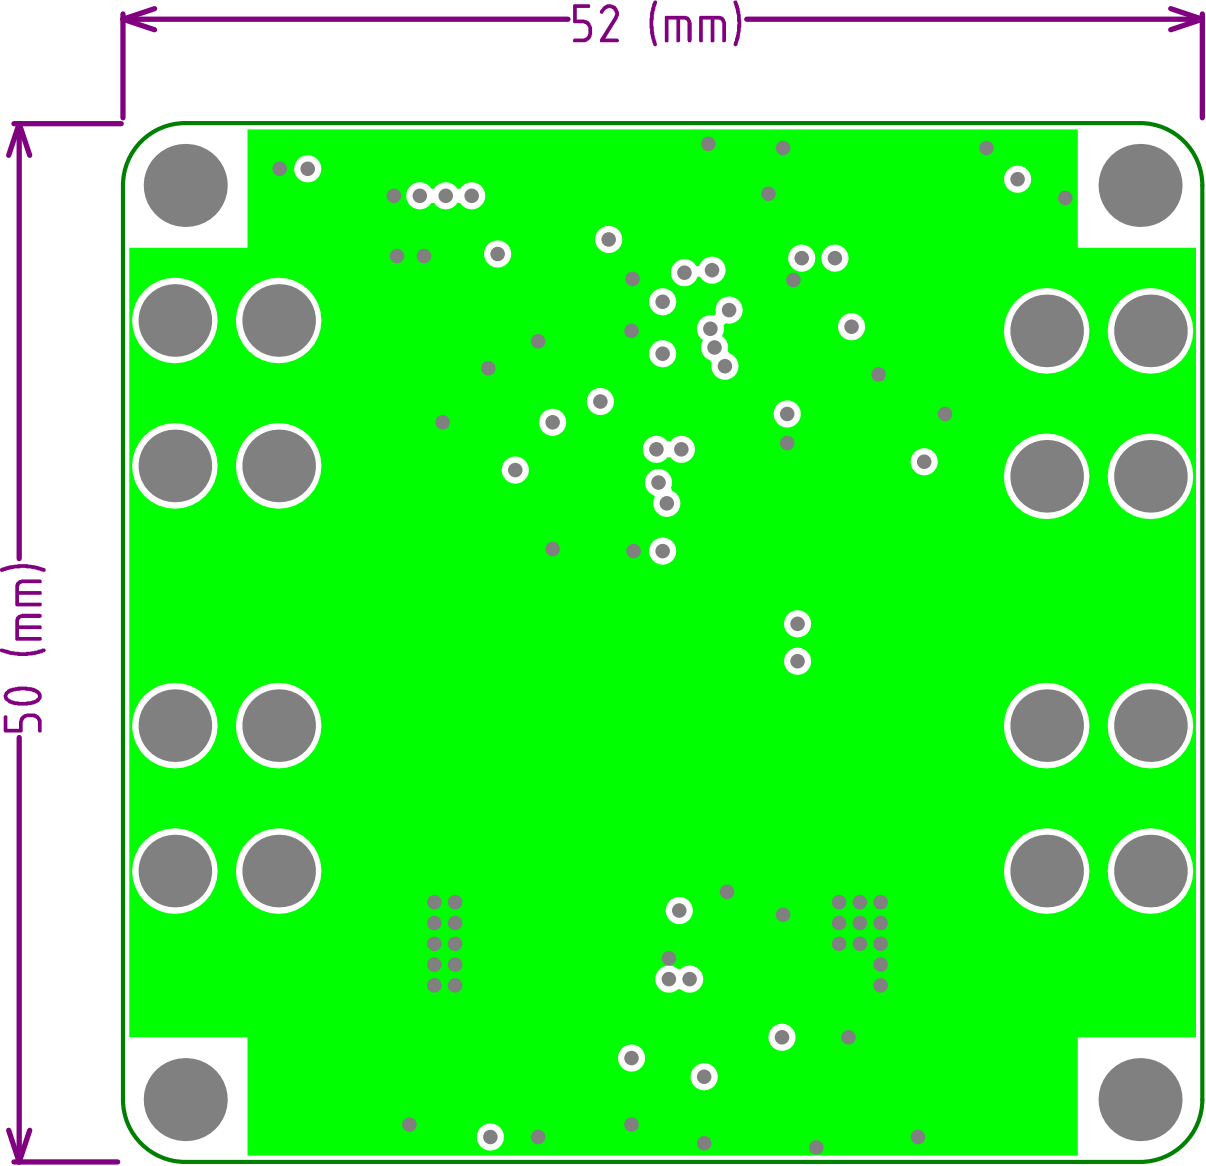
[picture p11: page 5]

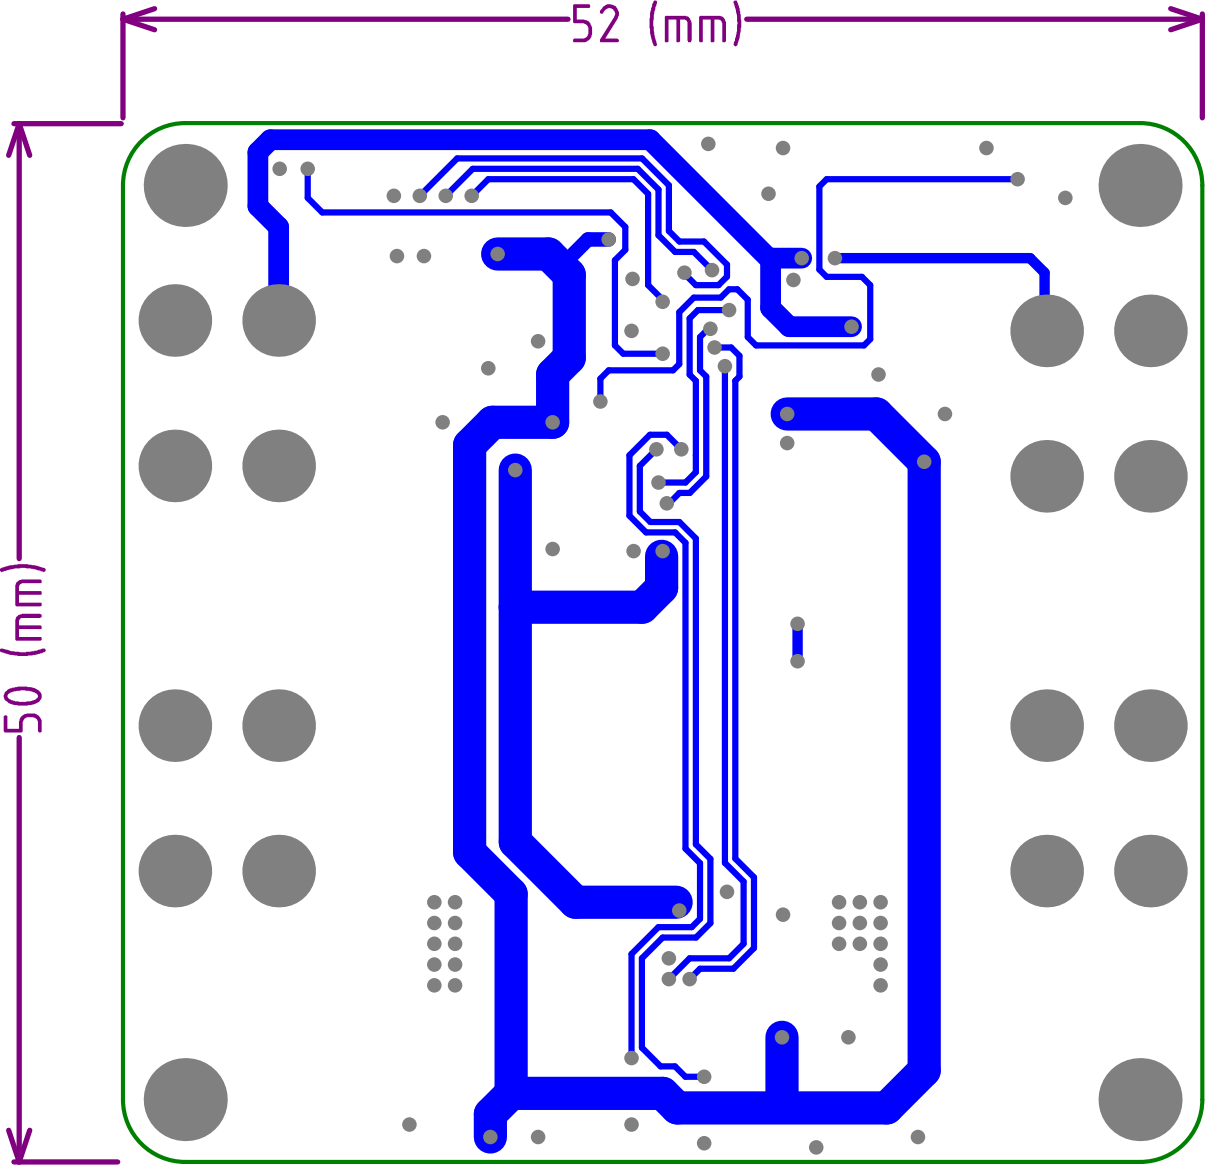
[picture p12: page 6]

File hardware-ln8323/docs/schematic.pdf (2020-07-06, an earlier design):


Author | Ilya Galkin | Buck-boost digital converter with CC/CV up to 20W

Date | 05.07.2020

Manufacturer | PCBway

Page | 1

Total pages | 2

Size page | A2

Materials | FR-4


Цепь | Конт.

PC13 4 | VDD

SWDIO | 2

SWCLK | 3
4 | UART1-TX TX

SWCLK 37 | 24

NRST 7 | | 36 | 0.1μF

GND | 5

BOOT0 44

Author | Ilya Galkin | Buck-boost digital converter with CC/CV up to 20W

Date | 05.07.2020

Manufacturer | PCBway

Page | 2

Total pages | 2

Size page | A3

Materials | FR-4





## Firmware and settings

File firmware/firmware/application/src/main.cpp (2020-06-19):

/********************************************************************************
 * project     DC/DC buck-boost converter with digital control on the STM32F334 *
 *                                                                              *
 * file        main.cpp                                                         *
 * author      Ilya Galkin                                                      *
 * date        17.06.2020                                                       *
 * brief       Main program body                                                *
 *                                                                              *
 ********************************************************************************/

/********************************************************************************
 * Include 
 ********************************************************************************/

#include "main.h"

/********************************************************************************
 * Main program body
 ********************************************************************************/

int main (void) {

    Periphery::Init();
    Application::Init();

    while(1) {}
}

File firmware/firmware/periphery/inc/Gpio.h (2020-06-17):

/********************************************************************************
 * Class        Control and settings for ports input/output                     *
 *                                                                              *
 * file         Gpio.h                                                          *
 * author       Ilya Galkin                                                     *
 * date         11.05.2020                                                      *
 *                                                                              *
 ********************************************************************************/

#pragma once

/********************************************************************************
 * Include 
 ********************************************************************************/

#include "stm32f3xx.h"

/********************************************************************************
 * Class Gpio
 ********************************************************************************/

class Gpio {

    public:
        enum class Mode:int {
            analog = 0b11, input = 0b00, output = 0b01, outputAF = 0b10
        };

        enum class Type:int {
            PP, OD
        };
        
        enum class Speed:int {
            low = 0, medium = 0b01, high = 0b10, veryHigh = 0b11
        };

        enum class Pupd:int {
            noPull = 0, pullUp = 0b01, pullDown = 0b10
        };

        enum class AF:int {
            af0, af1, af2, af3, af4, af5, af6, af7, af8, af9, af10, af11, af12, af13, af14, af15
        };

    public:
        template<uint8_t ... pins>
        static inline void Init (GPIO_TypeDef * port = GPIOA, Mode m = Mode::input, Type t = Type::PP, Speed s = Speed::low, Pupd p = Pupd::noPull, AF a = AF::af0) {

            if (port == GPIOA)
                RCC->AHBENR  |= RCC_AHBENR_GPIOAEN;
            if (port == GPIOB)
                RCC->AHBENR  |= RCC_AHBENR_GPIOBEN;
            if (port == GPIOC)
                RCC->AHBENR  |= RCC_AHBENR_GPIOCEN;
            if (port == GPIOD)
                RCC->AHBENR  |= RCC_AHBENR_GPIODEN;
            if (port == GPIOF)
                RCC->AHBENR  |= RCC_AHBENR_GPIOFEN;


            uint32_t temp1 = 0, temp2 = 0;
            ((temp1 |= (0b11 << (2*pins))), ... );
            port->MODER &= ~(temp1);
            temp1 = 0;
            ((temp1 |= int(m) << (2*pins)), ... );
            port->MODER |= temp1;

            temp1 = 0;
            ((temp1 |= (0b1 << (pins))), ... );
            port->OTYPER &= ~(temp1);
            temp1 = 0;
            ((temp1 |= (int(t) << (pins))), ... );
            port->OTYPER |= temp1;

            temp1 = 0;
            ((temp1|=(0b11 << (2*pins))), ... );
            port->OSPEEDR &= ~(temp1);
            temp1 = 0;
            ((temp1 |= (int(s) << (2*pins))), ... );
            port->OSPEEDR |= temp1;

            temp1 = 0;
            ((temp1 |= (0b11 << (2*pins))), ... );
            port->PUPDR &= ~(temp1);
            temp1 = 0;
            ((temp1 |= (int(p) << (2*pins))), ... );
            port->PUPDR |= temp1;

            temp1 = 0;
            (((pins < 8?temp1:temp2) |= (0b11 << (4*(pins-(pins<8?0:8))))), ... );
            port->AFR[0] &= ~temp1;
            port->AFR[1] &= ~temp2;

            temp1 = 0;
            temp2 = 0;
            (((pins < 8?temp1:temp2) |= (int(a) << (4*(pins-(pins<8?0:8))))), ... );
            port->AFR[0] |= temp1;
            port->AFR[1] |= temp2;

        }

        template<uint32_t ... pins>
        static inline void Set (GPIO_TypeDef* port) {
            uint32_t temp = 0;
            ((temp |= 1<<pins), ...);
            port->BSRR = temp;
        }

        template<uint32_t ... pins>
        static inline void Toggle (GPIO_TypeDef* port) {
            uint32_t temp = 0;
            ((temp |= 1<<pins), ...);
            port->ODR ^= temp;
        }

        template<uint32_t ... pins>
        static inline void Reset (GPIO_TypeDef* port) {
            uint32_t temp = 0;
            ((temp |= 1<<(pins+16)), ...);
            port->BSRR = temp;
        }

    private:

};

/********************************* END OF FILE **********************************/

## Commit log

2020-05-23 docs: Добавил документацию на МК и на модуль HRPWM
2020-05-26 new: Завершил проект buck-boost преобразователя. v.1.0
    [buck-boost.PrjPcb, converter.SchDoc, custom-lib.PcbLib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]
2020-05-26 docs: Добавил pinout на МК для v1.0
2020-05-26 docs: Сгенерировал КД и ВОМ на v1.0 buck-boost
    [bom.xlsx]
2020-05-26 docs: Добавил исключения папок preview и history для AD
2020-05-26 docs: Добавил описание и сведения о проекте
2020-05-28 fix: Уменьшил диаметр крепления с 3 до 2 мм. Добавил реперные точки
    [buck-boost.PrjPcb, pcb.PcbDoc]
2020-05-28 fix: Обновил 3d модель с учетом последних изменений
2020-06-17 new: Создал проект на С++, настроил основную периферию для buck-boost
2020-06-17 docs: Добавил исключение для временных файлов дебага
2020-06-18 new: Завершил настройку АЦП, данные читаются
2020-06-18 new: Написал методы для настройки buck-boost и методы для установки заполнения
2020-06-18 new: Создал заготовки под написание логики приложения
2020-06-19 new: Завершил класс преобразования сырых данные АЦП в напряжения и токи
2020-06-19 new: Реализовал функцию UVLO при включение питания
2020-06-19 new: Создал папку dsp для функций ЦОС и ТАУ
2020-06-19 new: Удалил из обработчика АЦП лишний функционал, выборка 1 кГц
2020-06-19 new: Увеличил частоту выборки АЦП с 1 до 10 кГц
2020-06-19 new: Добавил установку ног ШИМ в ноль прямо в момент старта
2020-06-19 new: Удалил все лишнее, оставил лишь методы инициализации
2020-06-19 new: Завершил управление buck-boost преобразователем и протестировал
2020-06-19 new: Изменил имя проекта на корректное buck_boost, поправил настройки
2020-06-19 fix: Добавил префикс Get для функций вычисления напряжений и токов
    [Application.cpp, Feedback.h]
2020-06-20 docs: Обновил описание проекта после проверки работоспособности преобразователя
2020-06-20 docs: Добавил явное указание используемого ЯП
2020-06-20 fix: Преобразовал все табы в пробелы, отформатировал код
    [Application.cpp]
2020-06-21 fix: Увеличил аппаратный dead-time драйвера, R9 и R10 поставил 120 кОм
    [bom.xlsx, buck-boost.PrjPcb, converter.SchDoc]
2020-06-28 docs: Добавил исключение папки build для firmware
2020-06-28 new: Реализовал более эффективный алгоритм управления buck-boost
    Вместо фиксированного значения ШИМ для boost, реализовал
    выбор более оптимального значения в зависимости от
    значения входного напряжения
2020-06-28 fix: Изменил модификатор переменной периода ШИМ на безопасный constexpr
2020-06-28 docs: Исправил описание для класса PidController
2020-06-28 new: Реализовал CC/CV режим и протестировал его работу
2020-06-28 new: Реализовал зарядное устройство для Li-ion 2S на 1А
2020-06-30 new: Повысил стабильность запуска в CV режиме без нагрузки
    Добавил отдельное условие перехода из CC режима в CV,
    по минимальному току и по приближению к заданному
    напряжению на выходе
2020-07-05 new: Начал разработку v2.0. Завершил разработку схемы
    [buck-boost.PrjPcb, converter.SchDoc, custom-lib.PcbLib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]
2020-07-05 fix: Добавил LDO на 5В и запитал с него драйвер, ибо 15В не держит
    [converter.SchDoc]
2020-07-05 new: Завершил проектирование платы v2.0 на базе LN8323
    [buck-boost.PrjPcb, converter.SchDoc]
2020-07-05 docs: Обновил документацию и КД на новую v2.0 на LN8323
    [bom.xlsx]
2020-07-06 fix: Поменял дроссель на дешевый SP105. Обновил КД после изменений
    [bom.xlsx, buck-boost.PrjPcb, converter.SchDoc]
2020-07-06 new: Слил 2 версии схемы и платы в одну ветку
    В ветку master добавил обе версии папки hardware
    для версий на PN7725 и LN8323
    [bom.xlsx, buck-boost.PrjPcb, converter.SchDoc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]
2020-07-14 new: Изменил значения gain и сопротивление шунта для новой версии железа
2020-07-20 new: Добавил папку с hw для первой версии платы на 4-х ключах
    [bom.xlsx, buck-boost.PrjPcb, converter.SchDoc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]
2020-09-01 new: Портировал последние изменения из gitLab и открыл проект
